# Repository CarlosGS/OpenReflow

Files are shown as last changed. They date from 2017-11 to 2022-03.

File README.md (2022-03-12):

# OpenReflow
Simple reflow oven controller based on ESP8266

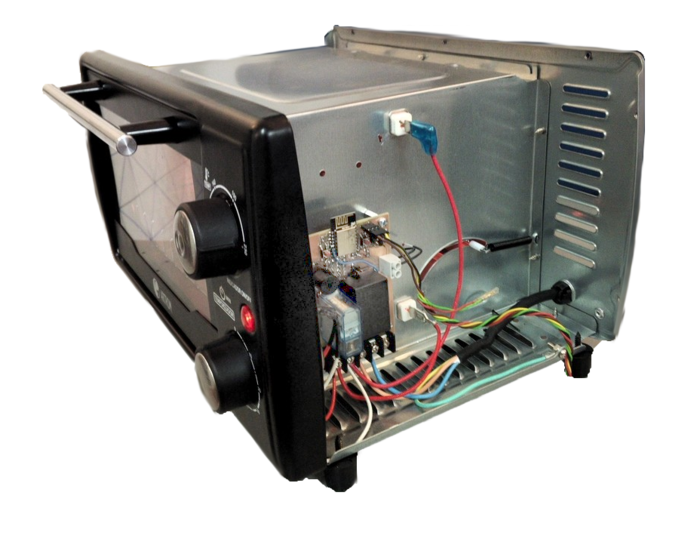
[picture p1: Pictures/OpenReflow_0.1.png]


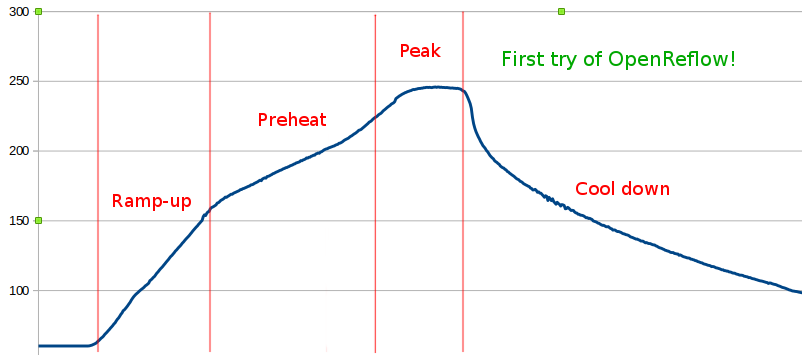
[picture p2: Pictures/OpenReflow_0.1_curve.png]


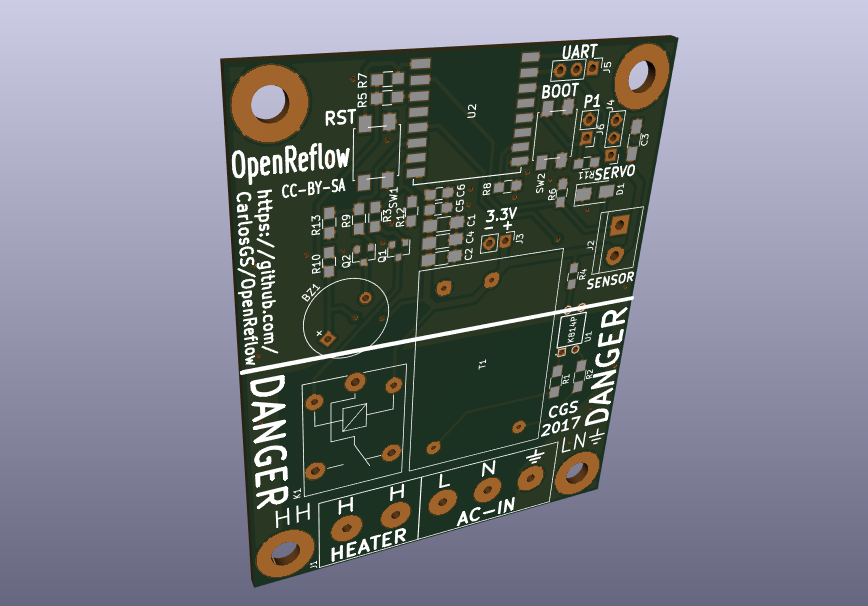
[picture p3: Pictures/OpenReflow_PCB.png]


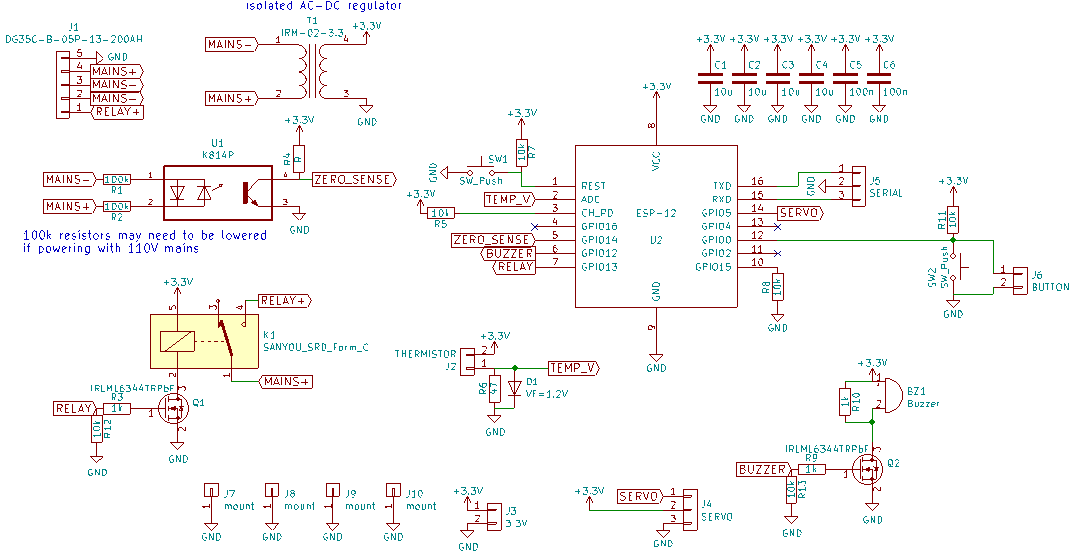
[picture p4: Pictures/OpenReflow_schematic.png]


# NOT RECOMMENDED FOR NEW BUILDS!

Please note that for the temperature sensor, I used a voltage divider to read a PT100 element. This makes it necessary to manually calibrate, and even then it wouldn't be as accurate as using a proper RTC reading chip (i.e. MAX31865).

Also the "zero crossing" detector wasn't really necessary for the small wattage and slow pulses involved (at most 1500W at 1Hz). It just adds complexity and makes the board more dangerous by mixing digital and live tracks.

In the end I think it would be more simple to just flash a standard Sonoff switch and wire an external temperature sensor module.

# More information can be found in PCBway

<https://www.pcbway.com/project/shareproject/OpenReflow.html>

# License

Software is GPLv3, Hardware (PCB) is CC-BY-SA.

Author: Carlos Garcia Saura (@CarlosGS)

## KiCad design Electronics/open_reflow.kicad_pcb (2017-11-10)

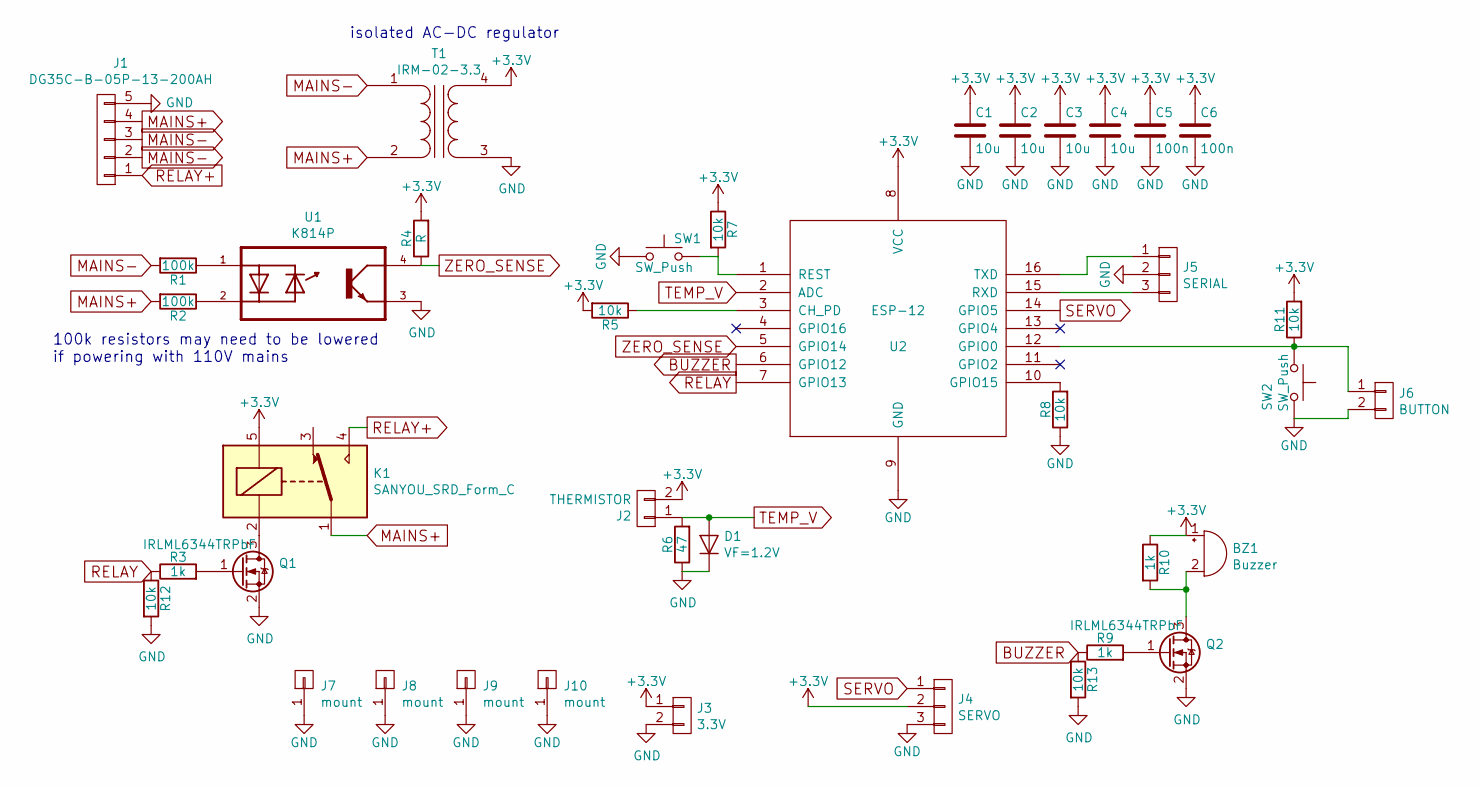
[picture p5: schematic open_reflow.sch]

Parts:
BZ1: Buzzer; MagneticBuzzer_ProSignal_ABI-009-RC
C1, C2, C3, C4: 10u; C_1206_HandSoldering
C5, C6: 100n; C_0805_HandSoldering
D1: VF=1.2V; D_SMA
J1: DG35C-B-05P-13-200AH; TerminalBlock_bornier-5_P5.08mm
J2: THERMISTOR; TerminalBlock_bornier-2_P5.08mm
J3: 3.3V; Pin_Header_Straight_1x02_Pitch2.54mm
J4: SERVO; Pin_Header_Straight_1x03_Pitch2.54mm
J5: SERIAL; Pin_Header_Straight_1x03_Pitch2.54mm
J6: BUTTON; Pin_Header_Straight_1x02_Pitch2.54mm
J7, J8, J9, J10: mount; MountingHole_4.5mm_Pad
K1: SANYOU_SRD_Form_C; Relay_SPDT_SANYOU_SRD_Series_Form_C
Q1, Q2: IRLML6344TRPbF; SOT-23
R1, R2: 100k; R_1206_HandSoldering
R3, R9, R10: 1k; R_0805_HandSoldering
R4: R; R_0805_HandSoldering
R5, R7, R8, R11, R12, R13: 10k; R_0805_HandSoldering
R6: 47; R_0805_HandSoldering
SW1, SW2: SW_Push; smd_button
T1: IRM-02-3.3; ACDC-Converter_MeanWell-IRM-02-x
U1: K814P; DIP762W50P254L458H480Q4
U2: ESP-12

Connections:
+3V3: BZ1.1 (-), C1.1, C2.1, C3.1, C4.1, C5.1, C6.1, J2.2, J3.1, J4.2, K1.5, R4.2, R5.2, R7.1, R10.1, R11.2, T1.4 (SB), U2.8 (VCC)
BUZZER: R9.1, R13.1, U2.6 (GPIO12)
GND: C1.2, C2.2, C3.2, C4.2, C5.2, C6.2, D1.1 (K), J1.5, J3.2, J4.3, J5.2, J6.2, J7.1, J8.1, J9.1, J10.1, Q1.2 (S), Q2.2 (S), R6.1, R8.1, R12.2, R13.2, SW1.1, SW2.2, T1.3 (SA), U1.3, U2.9 (GND)
MAINS+: J1.4, K1.1, R2.2, T1.2 (AB)
MAINS-: J1.2, J1.3, R1.2, T1.1 (AA)
unnamed: BZ1.2 (+), Q2.3 (D), R10.2
unnamed: J5.1, U2.16 (TXD)
unnamed: J5.3, U2.15 (RXD)
unnamed: J6.1, R11.1, SW2.1, U2.12 (GPIO0)
unnamed: K1.2, Q1.3 (D)
unnamed: Q1.1 (G), R3.2
unnamed: Q2.1 (G), R9.2
unnamed: R1.1, U1.1
unnamed: R2.1, U1.2
unnamed: R5.1, U2.3 (CH_PD)
unnamed: R7.2, SW1.2, U2.1 (REST)
unnamed: R8.2, U2.10 (GPIO15)
RELAY: R3.1, R12.1, U2.7 (GPIO13)
RELAY+: J1.1, K1.4
SERVO: J4.1, U2.14 (GPIO5)
TEMP_V: D1.2 (A), J2.1, R6.2, U2.2 (ADC)
ZERO_SENSE: R4.1, U1.4, U2.5 (GPIO14)

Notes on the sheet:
100k resistors may need to be lowered if powering with 110V mains
isolated AC-DC regulator

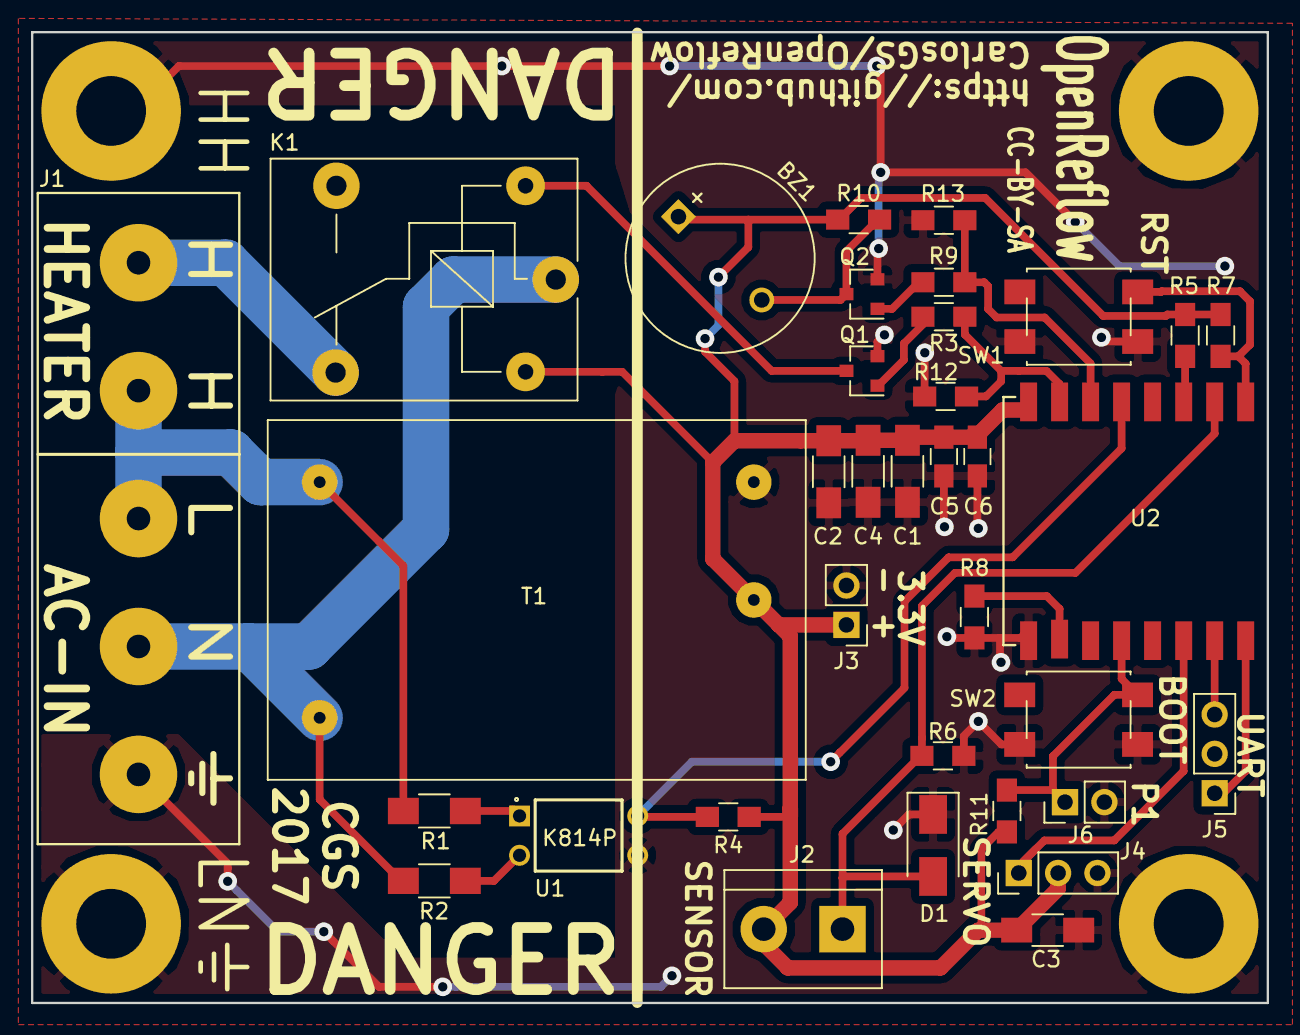
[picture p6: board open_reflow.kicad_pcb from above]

Board: 2 copper layers, 79.7 x 62.6 mm, 39 parts (0 on the bottom side), 22 nets.

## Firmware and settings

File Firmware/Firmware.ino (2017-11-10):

// OpenReflow controller
// Made by @CarlosGS
// https://github.com/CarlosGS/OpenReflow
// CC-BY-SA license

#include "ESP8266WiFi.h"

#define BUZZER_PIN 12
void init_buzzer() {
  pinMode(BUZZER_PIN, OUTPUT);
  digitalWrite(BUZZER_PIN, LOW);
}
void play_tone(int frequency, int duration_ms) {
  tone(BUZZER_PIN, frequency, duration_ms);
  delay(duration_ms+10);
  digitalWrite(BUZZER_PIN, LOW);
}
void play_startup() {
  play_tone(400, 200);
  play_tone(600, 200);
  play_tone(800, 600);
}
void play_error() {
  play_tone(800, 600);
  delay(200);
  play_tone(800, 600);
  delay(200);
  play_tone(800, 600);
  delay(200);
  play_tone(800, 600);
  delay(200);
}
void play_reflow_begin() {
  play_tone(400, 100);
  play_tone(600, 100);
  play_tone(800, 100);
  
  play_tone(400, 100);
  play_tone(600, 100);
  play_tone(800, 100);
  
  play_tone(400, 100);
  play_tone(600, 100);
  play_tone(800, 600);
}
void play_reflow_end() {
  play_tone(800, 200);
  delay(50);
  play_tone(800, 1000);
}

#define RELAY_PIN 13
#define ZERO_CROSS_PIN 14
void init_relay() {
  pinMode(ZERO_CROSS_PIN, INPUT);
  pinMode(RELAY_PIN, OUTPUT);
  digitalWrite(RELAY_PIN, LOW);
}
void set_relay(bool state) {
  while(digitalRead(ZERO_CROSS_PIN) == HIGH) yield();
  while(digitalRead(ZERO_CROSS_PIN) == LOW) yield();
  digitalWrite(RELAY_PIN, state);
}

void setup() {
  delay(1000);
  Serial.begin(115200);
  Serial.println("\n\n ____________________");
  Serial.println(    "| |  ____________    |");
  Serial.println(    "| | |            | O |");
  Serial.println(    "| | | OpenReflow |   |");
  Serial.println(   "\\ | |____________| O |");
  Serial.println(   " \\|__________________|\n");
  
  Serial.println("Initializing pins...\n");

  init_relay();
  init_buzzer();
  
  Serial.println("Setting up AP...\n");
  WiFi.softAP("OpenReflow", "OpenReflow");

  Serial.println("All set! Now connect your phone to the OpenReflow WiFi access point!\n");
  play_startup();
}

float mapf(float x, float in_min, float in_max, float out_min, float out_max)
{
  return (x - in_min) * (out_max - out_min) / (in_max - in_min) + out_min;
}

float Vin = 3.3; // volts
float R2 = 50; // ohms

float temp() {
  double Vout_filt = 0;
  int N = 100;
  for(int i=0; i<N; i++) {
    Vout_filt += analogRead(A0);
    delay(1);
  }
  Vout_filt /= (double)N;
  float Vout = mapf(Vout_filt, 227,896.95, 0.202,0.833);// Calibrated ADC values
  float R1 = R2*((Vin/Vout)-1);
  float temp_degreesC = ((R1/100)-1)/0.00385;
  return temp_degreesC;
}

float value_filtered = 0;

int reflow_phase = 0;

float last_temperature = 0;
void loop() {
  int heating = 0;
  float temperature = temp();
  float temp_speed = (temperature-last_temperature)*2;// the 2 scales to degreesC/second

  switch(reflow_phase) {
    case 0: // Ramp-up
      heating = temp_speed < 3; // max 3degC/s
      if(temperature > 150) {
        reflow_phase = 1;
        play_startup();
      }
      break;
    case 1: // Preheat
      heating = temp_speed < 0.8; // max 0.8degC/s
      if(temperature > 200) {
        reflow_phase = 2;
        play_reflow_begin();
      }
      break;
    case 2: // Reflow
      heating = 1;
      if(temperature > 235) {
        reflow_phase = 3;
        play_reflow_end();
      }
      break;
    case 3: // Cool
      heating = 0;
      break;
  }
  set_relay(heating);
  Serial.print(millis());
  Serial.print("\t");
  Serial.print(reflow_phase);
  Serial.print("\t");
  Serial.print(temperature);
  Serial.print("\t");
  Serial.println(heating);
  delay(500);
  last_temperature = temperature;
}

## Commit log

2017-11-10 Added project sources
    [open_reflow-B.Cu.gbr, open_reflow-B.Mask.gbr, open_reflow-Edge.Cuts.gbr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]
2017-11-10 Added reflow profile & circuit diagram
2017-11-10 Added PCB picture
